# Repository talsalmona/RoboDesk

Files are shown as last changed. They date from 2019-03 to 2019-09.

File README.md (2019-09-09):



# RoboDesk
Arduino code for LOGICDATA protocol and remote handset hacking for automated standing desk

(LogicData data sheet can be found [here](https://web.archive.org/web/20180514132622/http://www.logicdata.net/wp-content/uploads/2017/05/Datasheet_Compact_English-Rev4.pdf))

Based on the great work of [mtfurlan](https://github.com/mtfurlan/RoboDesk) and [phord](https://github.com/phord/RoboDesk)

# Demo
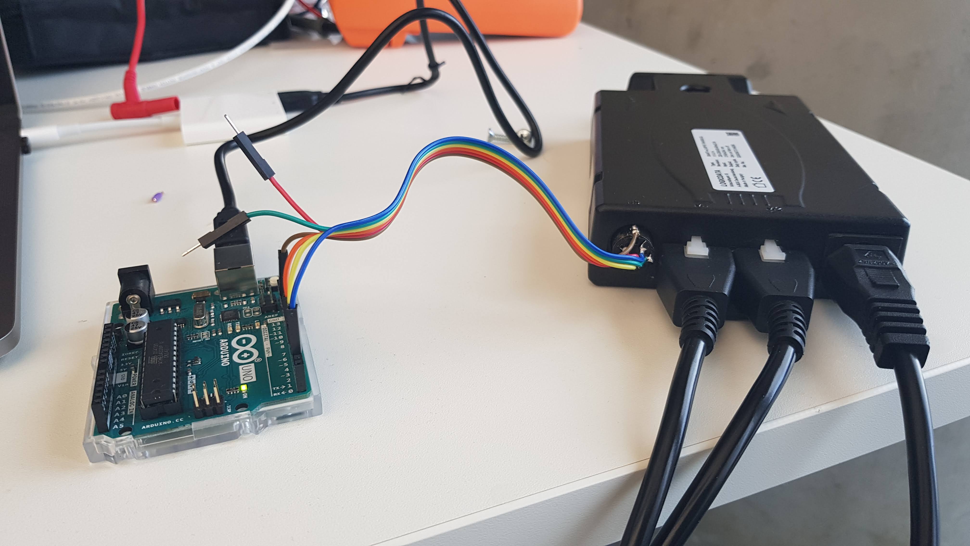
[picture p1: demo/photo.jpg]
demo

demo (https://www.youtube.com/watch?v=RAITo_iL8os)

# Current Functionality
* Preset low / high position by clicking up and down buttons simulataniously - audio feedback provided for successful storing of position. Last direciton in which the table moved defines if the high or low position is storred.
* Double tap up / down buttons to go to the high / low preset position

# Board
Currently works with an Arduino Uno or Nano because it requires 5v logic.

# Step by Step Setup
## Buy the Following Components
* [DIN 7 connector](https://www.aliexpress.com/item/OOTDTY-1Pc-Male-Female-DIN-Plug-Socket-Connector-3-4-5-6-7-8-PIN-Chassis/32860020971.html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) - Make sure to get the 7 pins
* Some [header wires](https://www.aliexpress.com/item/40pcs-lot-10cm-2-54mm-1pin-Female-to-Female-jumper-wire-Dupont-cable/32378478740.html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)
* Optional [Piezo Buzzer](https://www.aliexpress.com/item/5pcs-3-V-Active-Buzzer-Electromagnetic-SOT-Laminate-Tube-3-V-Is-The-Real-Thing/32651928778.html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)
* [Soldering iron](https://www.aliexpress.com/item/220V-60W-Portable-Electric-Soldering-Iron-Adjustable-Temperature-Solder-Iron-5pcs-Tips-Welding-Repair-Tool-kit/32815385816.html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) - or borrow from a friend
* [Arduino Nano](https://www.aliexpress.com/item/Freeshipping-Nano-3-0-controller-compatible-for-arduino-nano-CH340-USB-driver-NO-CABLE/32341832857.html)

## Prepare the DIN7 Connector
1. Take note of the following diagram - it represents the pins when looking at the connector from the back (where you would need to solder the wires)

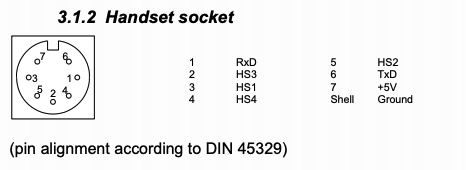
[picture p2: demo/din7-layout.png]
DIN7-wiring


2. You will need to wire +5V, Ground, HS1, HS2 and RxD.

3. Cut one end of the wires and solder onto the DIN7 connector

4. Optionally, use epoxy glue to make sure the soldering holds

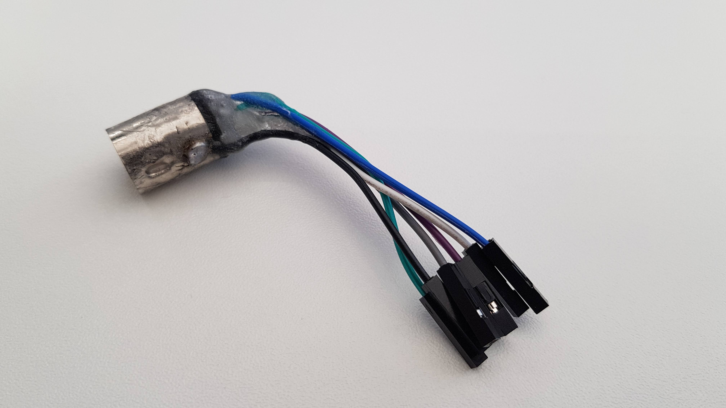
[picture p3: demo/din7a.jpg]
DIN7-a

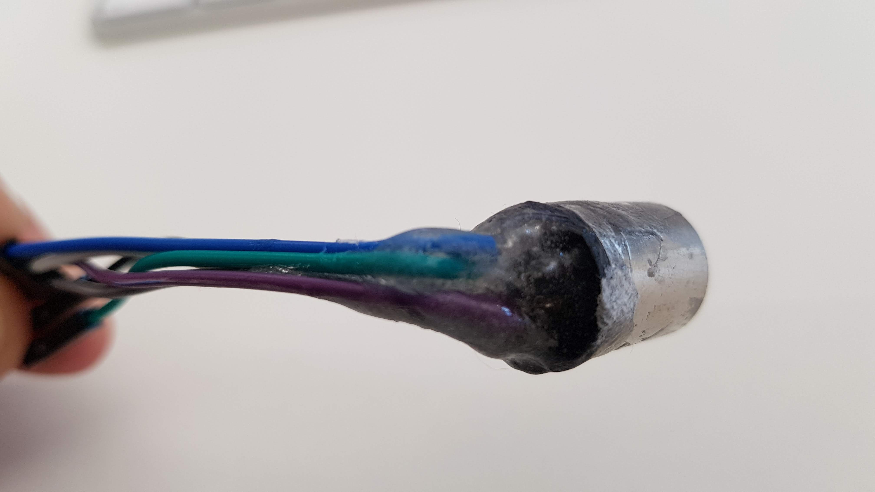
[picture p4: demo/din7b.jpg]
DIN7-b


## Wiring the Board
Wire the board according to the mapping that can be found in [pins.h](pins.h)

## Upload the Code
The easiest way to upload the code is to open it in the Arduino IDE and flash it onto the board.

## Print a Case (WIP)
Use a 3D printer to print a case
Models are available in the [box](https://github.com/talsalmona/RoboDesk/blob/master/box) folder

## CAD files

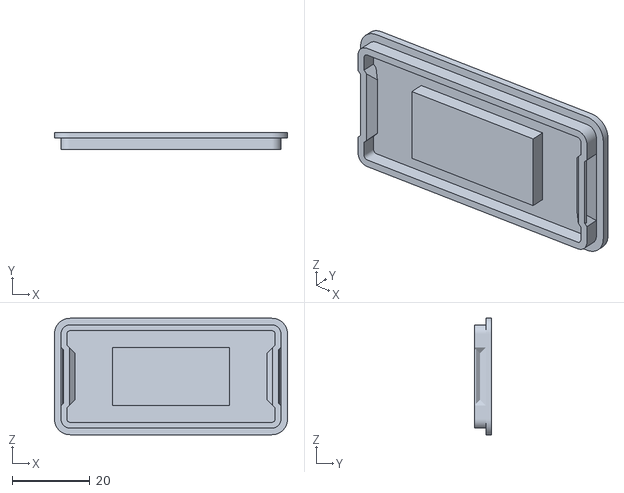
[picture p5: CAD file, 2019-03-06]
box/base.stl
60.0 x 4.50 x 30.0

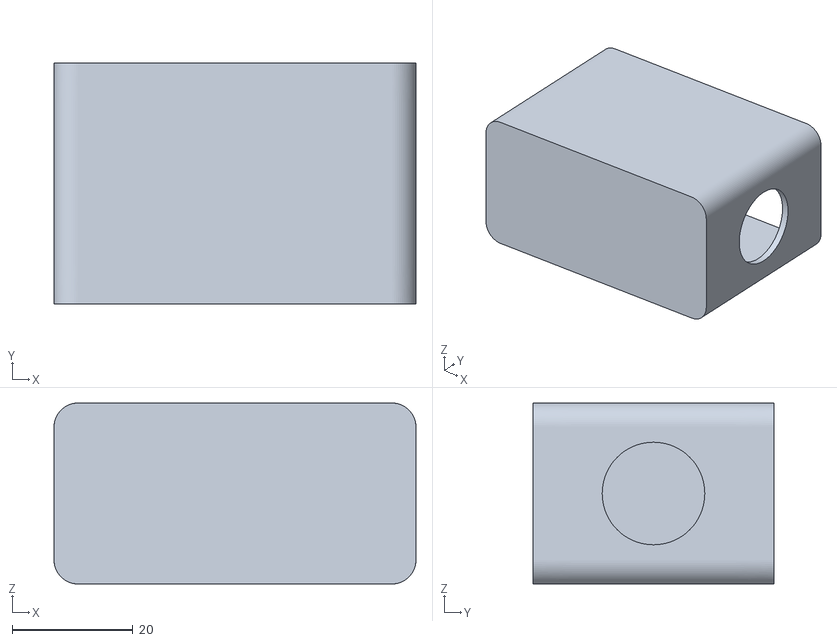
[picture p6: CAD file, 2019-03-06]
box/top.stl
60.0 x 40.0 x 30.0

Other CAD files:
box/box.f3d

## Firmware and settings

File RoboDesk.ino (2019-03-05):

#include "pins.h"
#include "LogicData.h"
#include "buttons.h"
#include <EEPROM.h>


//#define DISABLE_LATCHING

#define LOWEST 60
#define HIGHEST 130

//Initial values for when we haven't saved a preset before
unsigned int HEIGHT_HIGH = HIGHEST;
unsigned int HEIGHT_LOW  = LOWEST;

unsigned long last_signal = 0;
unsigned long last_latch = 0;
unsigned int last_direction = -1;

LogicData ld(INTF_TX);

uint8_t height;
uint8_t target;

//-- Pass through mode sends input signal straight to output
inline void passThrough(uint8_t out, uint8_t in) {
  digitalWrite(out, digitalRead(in));
}

// Pass module TX straight through to interface RX
void dataPassThrough() {
  if (!ld.is_active()) passThrough(INTF_TX, MOD_TX);
}

//-- Buffered mode parses input words and sends them to output separately
void dataGather() {
  digitalWrite(STATUS_LED, digitalRead(MOD_TX));
  ld.PinChange(HIGH == digitalRead(MOD_TX));
}



void setup() {
  
  pinMode(MOD_TX, INPUT);
//  digitalWrite(MOD_TX, HIGH); // turn on pullups (Needed for attiny85)

  pinMode(MOD_HS1, INPUT);
  pinMode(MOD_HS2, INPUT);
//  pinMode(MOD_HS3, INPUT);
//  pinMode(MOD_HS4, INPUT);

  pinMode(STATUS_LED, OUTPUT);
  pinMode(BUZZER, OUTPUT);

  dataGather();
  attachInterrupt(digitalPinToInterrupt(MOD_TX), dataGather, CHANGE);

  ld.Begin();
  delay(1000);

  Serial.begin(9600);
  Serial.println("Robodesk v1.0  build: " __DATE__ " " __TIME__);
  readPresets(); 
}

void buzz(long frequency, long length) {
  long delayValue = 1000000/frequency/2; // calculate the delay value between transitions
  //// 1 second's worth of microseconds, divided by the frequency, then split in half since
  //// there are two phases to each cycle
  long numCycles = frequency * length/ 1000; // calculate the number of cycles for proper timing
  //// multiply frequency, which is really cycles per second, by the number of seconds to 
  //// get the total number of cycles to produce
  for (long i=0; i < numCycles; i++){ // for the calculated length of time...
    digitalWrite(BUZZER,HIGH); // write the buzzer pin high to push out the diaphram
    delayMicroseconds(delayValue); // wait for the calculated delay value
    digitalWrite(BUZZER,LOW); // write the buzzer pin low to pull back the diaphram
    delayMicroseconds(delayValue); // wait again or the calculated delay value
  }
}

// Record last time the display changed
void check_display() {
  static uint32_t prev = 0;
  uint32_t msg = ld.ReadTrace();
  if (msg) {
    char buf[80];
    uint32_t now = millis();
    sprintf(buf, "%6lums %s: %s", now - prev, ld.MsgType(msg), ld.Decode(msg));
    Serial.println(buf);
    prev=now;
  }

  // Reset idle-activity timer if display number changes or if any other display activity occurs (i.e. display-ON)
  if (ld.IsNumber(msg)) {
    static uint8_t prev_number;
    auto display_num = ld.GetNumber(msg);
    height = display_num;
    
    if (display_num == prev_number) {
      return;
    }
    prev_number = display_num;
  }
  if (msg)
    last_signal = millis();

}

void latch(unsigned latch_pins, unsigned long max_latch_time = 15000) {
  set_latch(latch_pins, max_latch_time);

  // Restart idle timer when we get an interesting button
  last_latch = last_signal = millis();
}

// Time out stale latches
void hold_latch() {
  digitalWrite(STATUS_LED, is_latched());

  if (!is_latched()) return;

  if(height != target) {
    return;
  } else {
    display_buttons(get_latched(), "Hit Target");
    break_latch();
    return;
  }

  unsigned long delta = millis() - last_signal;

  unsigned long activity_timeout = (last_signal - last_latch < 2000) ? 2500 : 1500 ;

  // Let go after 500ms with no signals
  if (delta > activity_timeout) {
    display_buttons(get_latched(), "Idle");
    break_latch();
    return;
  }
}

// Check the buttons
void check_actions() {
  // quick-read buttons
  auto buttons = read_buttons();

  if (buttons && is_latched() && buttons != get_latched()) {
    //TODO: This doesn't trigger correctly all the time
    break_latch();

    display_buttons(buttons, "Interrupted");

    if(buttons == UP || buttons == DOWN) {
      // Drain all button events from handset interface so the interruption doesn't become a command
      clear_buttons();

      return;
    }
  }

  // read and display button changes
  static unsigned prev = NONE;
  buttons = read_buttons_debounce();


  // Ignore unchanged state
  if (buttons == prev) return;
  prev = buttons;

  // If we're latched here, then buttons is same as latched or else buttons is NONE
  switch (buttons) {
    case UP:
      target = HEIGHT_HIGH;
      Serial.print("Moving to height: ");
      Serial.println(target);
      last_direction = UP;
      if (is_latched()) {
        latch(buttons, 42000);
      } else {
        latch(buttons, 500);
      }
      break;

    case DOWN:
      //If it's latched, go till target
      target = HEIGHT_LOW;
      Serial.print("Moving to height: ");
      Serial.println(target);      
      last_direction = DOWN;
      if (is_latched()) {
        latch(buttons, 42000);
      } else {
        latch(buttons, 500);
      }
      break;

    case SET:
      writePresets();
      break;
    // Ignore all other buttons (NONE)
    default:
      return;
  }
}

void writePresets() {
  if (last_direction == UP) {  
    HEIGHT_HIGH = height;    
    EEPROM.write(0, height);
    Serial.print("Wrote high target: ");
    Serial.println(height);
    buzz(440, 300);
    buzz(493, 300);
    buzz(523, 300);
  }
  else if (last_direction == DOWN) {
    HEIGHT_LOW = height;
    EEPROM.write(100, height);
    Serial.print("Wrote low target: ");
    Serial.println(height);
    buzz(523, 300);
    buzz(493, 300);
    buzz(440, 300);
  }  
}

void readPresets() {
  HEIGHT_HIGH = EEPROM.read(0);
  HEIGHT_LOW = EEPROM.read(100);

  if (HEIGHT_HIGH > HIGHEST) HEIGHT_HIGH = HIGHEST;
  if (HEIGHT_LOW < LOWEST) HEIGHT_LOW = LOWEST;
  Serial.print("Read presets - high: ");
  Serial.print(HEIGHT_HIGH);
  Serial.print(", low: ");
  Serial.println(HEIGHT_LOW);

  buzz(440, 200);
  buzz(880, 200);
  buzz(440, 200);
}


void demo() {
  pinMode(MOD_HS1, OUTPUT);
  pinMode(MOD_HS2, OUTPUT);

  digitalWrite(MOD_HS1, HIGH);
  delay(4000);
  digitalWrite(MOD_HS1, LOW);

  digitalWrite(MOD_HS2, HIGH);
  delay(4000);
  digitalWrite(MOD_HS2, LOW);

}

void loop() {
  // Monitor panel buttons for our commands and take over when we see one

  check_actions();
  check_display();
  hold_latch();

  //demo();

}

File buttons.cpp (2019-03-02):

#include "buttons.h"
#include "Arduino.h"
#include "pins.h"

/** Interface to Robodesk handset buttons
 */

unsigned latched = 0;
unsigned long latch_time = 0;
unsigned long last_action = 0;

// Display anything that changed since last time
void display_buttons(unsigned buttons, const char * msg ) {
  static unsigned prev = 0;

  if (msg[0] || prev!=buttons) {
    Serial.print((buttons & HS1) ? " HS1" :  " ---");
    Serial.print((buttons & HS2) ? " HS2" :  " ---");

    switch (buttons) {
      case UP:    Serial.print("    UP          ");    break;
      case DOWN:  Serial.print("    DOWN        ");    break;
      case SET:   Serial.print("    SET         ");    break;
      case NONE:  Serial.print("    ----        ");    break;
      default:    Serial.print(" ** UNKNOWN **  ");    break;
    }
    Serial.println(msg);
  }
  prev = buttons;
}

bool is_latched() {
  return !!latched;
}

unsigned get_latched() {
  return latched;
}

void unlatch() {
  pinMode(MOD_HS1, INPUT);
  pinMode(MOD_HS2, INPUT);
}

void latch_pin(int pin)
{
#ifndef DISABLE_LATCHING
  pinMode(pin, OUTPUT);
  digitalWrite(pin, HIGH);
  delay(1);
#endif
}

void break_latch() {
  latched = 0;
  unlatch();
}

void apply_latch() {
  if (!latched) return;

  unsigned long delta = millis() - last_action;

  // Let go if latch timer expires
  if (delta > latch_time) {
    display_buttons(latched, "Timed out");
    break_latch();
    return;
  }

  // Re-assert latched buttons
  if (latched & HS1) latch_pin(MOD_HS1);
  if (latched & HS2) latch_pin(MOD_HS2);
}

void set_latch(unsigned latch_pins, unsigned long max_latch_time) {
  if (latched == latch_pins) {
    if (latch_time + max_latch_time > latch_time) {
      latch_time += max_latch_time;
    }
  } else {
    latched = latch_pins;
    latch_time = max_latch_time;
  }

  // Restart idle timer when we get an interesting button
  last_action = millis();

  // Activate the selected latch pins
  apply_latch();

  char buf[50];
  sprintf(buf, "Latched up to %lums", latch_time);
  display_buttons(latched, buf);
}

unsigned read_buttons() {
  unsigned buttons = 0;

  unlatch();
  if (digitalRead(MOD_HS1)) buttons |= HS1;
  if (digitalRead(MOD_HS2)) buttons |= HS2;
  apply_latch();

  return buttons;
}

bool draining = false;
void clear_buttons() {
  draining = true;
}

unsigned read_buttons_debounce() {
  static unsigned long debounce = 0;
  static unsigned prev_buttons = 0;

  unsigned diff = prev_buttons;
  prev_buttons = read_buttons();

  // Wait for interface to drain
  if (draining and prev_buttons) return NONE;
  draining = false;

  unsigned buttons = prev_buttons;

  // Ignore spurious signals
  if (diff && diff != prev_buttons) buttons = NONE;

  // Reset timer if buttons are drifting or unpressed
  if (!buttons) debounce = millis();

  // ignore signal until stable for 1-2ms
  if (millis()-debounce < 40) {
    buttons = NONE;
  }

  display_buttons(buttons);

  return buttons;
}

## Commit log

2018-11-21 Add status led and enclosure
    [robodesk-case.scad]
2019-02-28 Remapped pins, added buzzer and presets
    [RoboDesk.ino]
2019-03-06 Added a Fusion 360 box model (#3)
    * Added a Fusion 360 box model
    * Added the STL files for both parts
    [base.stl, box.f3d, robodesk-case.scad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]
